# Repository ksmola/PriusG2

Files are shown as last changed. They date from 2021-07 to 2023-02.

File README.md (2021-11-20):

# Prius G2 Inverter controller

## About 

Inverter control board for Toyota Prius Gen 2 (XW20) inverter. 
Some of the schematics are based on Johannes Huebner's work found [here](https://github.com/jsphuebner/inverter-hardware).
Running [openinverter](http://www.openinverter.org) firmware.

    - ESP32 on board
    - AMPSEAL connectors
    - 3D printed enclosure

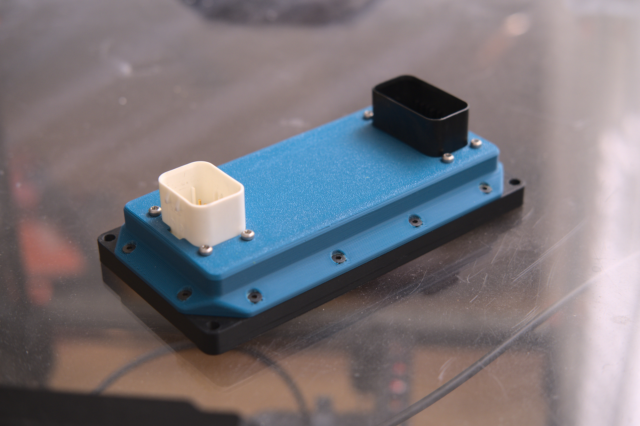
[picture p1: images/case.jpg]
case
 
## Prerequisites 

ESP32 needs [ported webinterface](https://github.com/Bedz01/esp32-web-interface-port)
Get latest openinverter firmware [here](https://github.com/jsphuebner/stm32-sine/releases)

## Pinout 

Pinout is documented on the bottom silk of the PCB

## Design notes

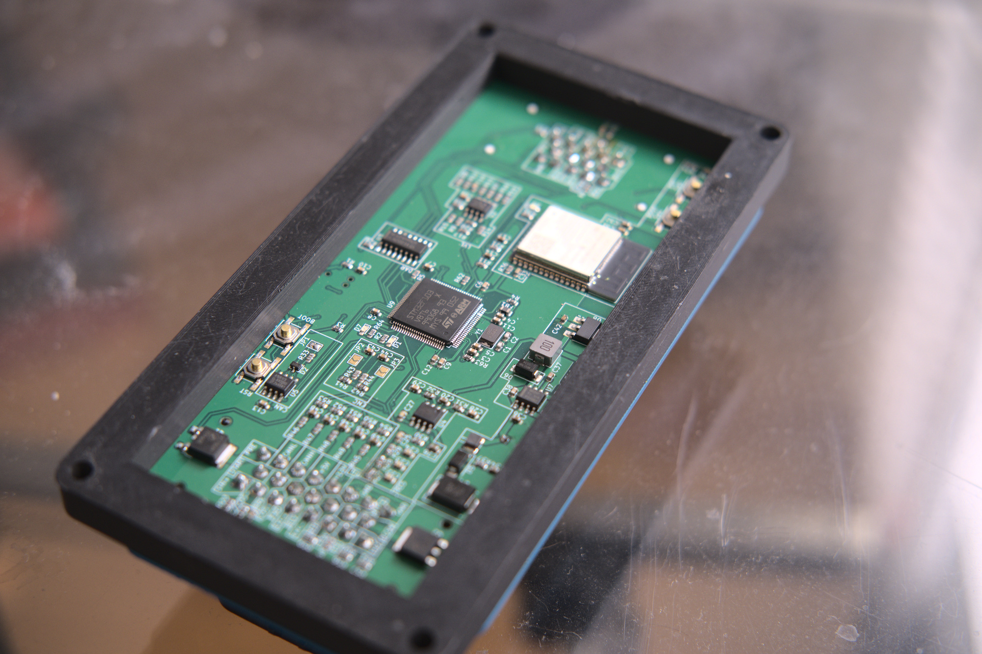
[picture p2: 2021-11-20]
images/board.jpg

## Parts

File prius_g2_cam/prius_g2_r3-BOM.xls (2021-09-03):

Comment | Designator | Package | LCSC Part
0603WAF1201T5E | R54,R53,R52,R51,R50 | R_0603_1608Metric | C22765
SMCJ36CA | D4 | D_SMC | C152081
CL10B102KB8NNNC | C44,C43,C16,C15,C19 | C_0603_1608Metric | C1588
0603WAF2200T5E | R23 | R_0603_1608Metric | C22962
AMS1117-3.3 | U8 | SOT-223-3_TabPin2 | C426566
0603WAF1003T5E | R17,R16,R10,R9,R8,R7 | R_0603_1608Metric | C25803
0603WAF5100T5E | R58,R55,R42,R41,R22 | R_0603_1608Metric | C23193
0603WAF1202T5E | R39 | R_0603_1608Metric | C22790
CL10A475KO8NNNC | C42,C34,C12 | C_0603_1608Metric | C19666
X50328MSB2GI | Y1 | Crystal_SMD_5032-2Pin_5.0x3.2mm | C115962
0603B104K250CT | C13,C11,C10,C9,C8,C7,C6,C5,C4,C3,C38,C29,C28 | C_0603_1608Metric | C83054
0603B104K250CT | C13,C11,C10,C9,C8,C7,C6,C5,C4,C3,C38,C29,C28 | C_0603_1608Metric | C83054
0603B103K500NT | C37 | C_0603_1608Metric | C57112
0603WAF1200T5E | R33 | R_0603_1608Metric | C22787
MWSA0503S-100MT | L2 | MWSA0503 | C408412
PESD1CAN-UX | D2 | SOT-323_SC-70 | C152727
LQH32PN2R2NN0L | L1 | L_1210_3225Metric | C86074
CL10A106KP8NNNC | C41,C40,C18,C32,C26 | C_0603_1608Metric | C19702
MHT192UBCT | D3,D1 | LED_0603_1608Metric_Castellated | C389520
E6Q0603URAC1UDA | D7 | LED_0603_1608Metric_Castellated | C375573
STM32F103VBT6 | U9 | LQFP-100_14x14mm_P0.5mm | C8314
RMC06031K1%N | R35,R2,R64 | R_0603_1608Metric | C269704
0603WAF3302T5E | R14,R12 | R_0603_1608Metric | C4216
LMR14020SDDAR | U7 | SOIC-8-1EP_3.9x4.9mm_P1.27mm_EP2.29x3mm | C187824
ESP32-WROOM-32D | U6 | ESP32-WROOM-32 | C473012
0603WAF3301T5E | R49,R48,R47,R46 | R_0603_1608Metric | C22978
TS-1187A-C-E-B | SW3,SW2,SW1,SW4 | SW_SPST_EVQQ2 | C318887
MCP6022T-I/SN | U2 | SOIC-8-1EP_3.9x4.9mm_P1.27mm_EP2.29x3mm | C57639
ULN2003ADR | U3 | SOIC-16_4.55x10.3mm_P1.27mm | C7512
0603WAF1502T5E | R15,R13 | R_0603_1608Metric | C22809
CL10B104KC8NNNC | C33,C31,C30 | C_0603_1608Metric | C15725
CL10A105KB8NNNC | C36,C20,C52,C51,C50,C49,C48,C47,C46,C45,C17,C14 | C_0603_1608Metric | C15849
CL10B223KB8NNNC | C27,C25,C24,C23,C22 | C_0603_1608Metric | C21122
0603WAF100KT5E | R37 | R_0603_1608Metric | C22936
TDA2822G-S08-R | U4 | SOIC-8-1EP_3.9x4.9mm_P1.27mm_EP2.29x3mm | C73296
CL10C331JB8NNNC | C39 | C_0603_1608Metric | C1664
0603WAF6802T5E | R40 | R_0603_1608Metric | C23231
SS34 | D6,D5 | D_SMA | C8678
AP9T18GH-HF | Q2,Q1 | TO-252-2 | C124546
TJA1051T/3/1J | U5 | SOIC-8_3.9x4.9mm_P1.27mm | C38695
0603WAF1002T5E | R26,R24,R21,R20,R19,R18,R11,R6,R5,R4,R63,R62,R61,R60,R57,R56,R44,R43,R38,R36,R34,R29,R30,R3,R1,R59 | R_0603_1608Metric | C25804
0603WAF4701T5E | R45,R32,R31,R25 | R_0603_1608Metric | C23162
CC0603JRNPO9BN200 | C2,C1 | C_0603_1608Metric | C105621
GZ2012D101TF | FB1 | C_0805_2012Metric | C1015
0603WAF3300T5E | R27 | R_0603_1608Metric | C23138
0603WAF6801T5E | R28 | R_0603_1608Metric | C23212

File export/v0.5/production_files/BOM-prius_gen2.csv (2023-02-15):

Comment | Designator | Footprint | LCSC
Ferrite_Bead | FB1 | C_0805_2012Metric | C1015
20pF | C1,C2 | C_0603_1608Metric | C105621
1uF 12mR | C23,C24 | C_0603_1608Metric | C106858
8MHz | Y1,Y2 | Crystal_SMD_5032-2Pin_5.0x3.2mm | C115962
100n | C16 | C_0603_1608Metric | C14663
SM15T33CA | D4 | D_SMC | C151281
.1uF | C20 | C_0603_1608Metric | C15725
1u | C15,C31,C38,C41 | C_0603_1608Metric | C15849
1n | C13,C14,C17,C39,C40 | C_0603_1608Metric | C1588
100nF | C10,C11,C12,C28,C3,C33,C4,C5,C7,C8,C9 | C_0603_1608Metric | C1590
120pF | C21,C22 | C_0603_1608Metric | C1643
330pF | C34 | C_0603_1608Metric | C1664
4.7uF | C29,C37,C6 | C_0603_1608Metric | C19666
1k | R5,R6 | R_0603_1608Metric | C21190
Q_NPN_BEC | Q1,Q3 | TSOT-23 | C2144
4r7 | R52,R53,R58,R59 | R_0603_1608Metric | C23164
510 | R11,R12,R7,R8 | R_0603_1608Metric | C23193
68k | R19,R20,R29 | R_0603_1608Metric | C23231
2.2uF | C26,C27 | C_0603_1608Metric | C23630
TestPoint | TP1,TP3,TP4,TP5,TP6,TP7,TP8,TP9 | TestPoint_Keystone_5000-5004_Miniature | C238124
1 | R26 | R_0603_1608Metric | C25086
100k | R14 | R_0402_1005Metric | C25741
10k | R1,R10,R13,R16,R18,R2,R22,R23,R27,R3,R30,R35,R42,R45,R46,R9 | R_0603_1608Metric | C25804
17.4k | R24,R51 | R_0603_1608Metric | C269466
10nF | C25,C32 | C_0603_1608Metric | C302008
22pF | C18,C19 | C_0603_1608Metric | C309441
22k | R21 | R_0603_1608Metric | C31850
2k2 | R47,R50,R54,R57 | R_0603_1608Metric | C325643
3r3 | R48,R49,R55,R56 | R_0603_1608Metric | C365471
2.2uH | L1 | L_1210_3225Metric | C36828
LED | D1 | LED_0603_1608Metric_Castellated | C40378
10u | L2 | MWSA0503 | C408412
~ | U9 | SOT-23-6 | C7519
Q_PNP_BEC | Q2,Q4 | TSOT-23 | C8326
D | D10,D7,D8,D9 | D_SOD-123 | C83528
LED | D2 | LED_0603_1608Metric_Castellated | C84264
schottky | D11 | D_SOD-123 | C8598
D_Schottky | D5,D6 | D_SMA | C8678
PESD1CAN-UX | D3 | SOT-323_SC-70 | C907839
AD2S1205YSTZ | U3 | QFP80P1200X1200X160-44N | C91729
10uF | C35,C36 | C_0603_1608Metric | C96446
4K7 | R17 | R_0603_1608Metric | C99782
12k | R28 | R_0603_1608Metric
SW_Push | SW1 | SW_SPST_EVQQ2
TJA1051T-3 | U4 | SOIC-8_3.9x4.9mm_P1.27mm
120 | R25 | R_0603_1608Metric
SW_Push | SW2 | SW_SPST_EVQQ2
SolderJumper_2_Open | JP2 | SolderJumper-2_P1.3mm_Open_TrianglePad1.0x1.5mm
SolderJumper_2_Open | JP3 | SolderJumper-2_P1.3mm_Open_TrianglePad1.0x1.5mm
SolderJumper_2_Open | JP1 | SolderJumper-2_P1.3mm_Open_TrianglePad1.0x1.5mm
AZ1117-3.3 | U6 | SOT-223-3_TabPin2
LMR14020 | U5 | SOIC-8-1EP_3.9x4.9mm_P1.27mm_EP2.29x3mm
MCP602 | U7 | SOIC-8-1EP_3.9x4.9mm_P1.27mm_EP2.29x3mm
100K | R41 | R_0603_1608Metric
10K | R43 | R_0603_1608Metric
100K | R34 | R_0603_1608Metric
33K | R38 | R_0603_1608Metric
33K | R36 | R_0603_1608Metric
15K | R37 | R_0603_1608Metric
100K | R33 | R_0603_1608Metric
100K | R31 | R_0603_1608Metric
100K | R32 | R_0603_1608Metric
15K | R39 | R_0603_1608Metric
100K | R40 | R_0603_1608Metric
10K | R44 | R_0603_1608Metric
ULN2003A | U2 | SOIC-16_4.55x10.3mm_P1.27mm
STM32F407VETx | U1 | LQFP-100_14x14mm_P0.5mm
AD8676xR | U8 | SOIC-8_3.9x4.9mm_P1.27mm
56uF | C30 | CP_Radial_D8.0mm_P3.50mm
Conn_01x23 | J3 | TE_776228-1
Conn_01x06 | J2 | Tag-Connect_TC2030-IDC-NL_2x03_P1.27mm_Vertical
Conn_01x14 | J4 | TE_776262-2
~ | J5 | PinSocket_1x05_P2.54mm_Vertical

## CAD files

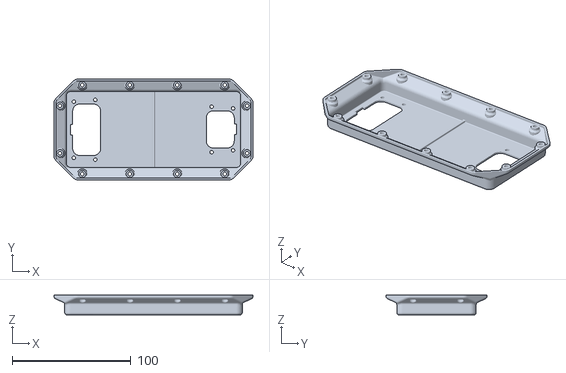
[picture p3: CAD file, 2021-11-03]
case_cad/top_shell.STL
167.8 x 85.0 x 16.7

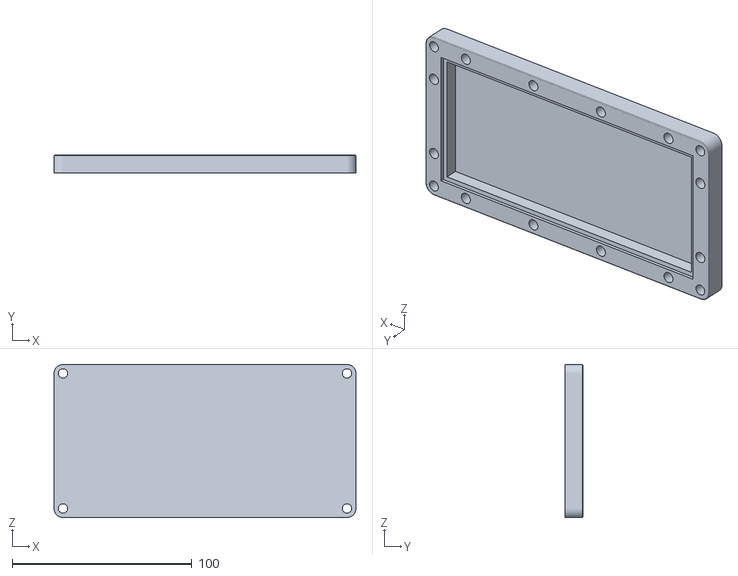
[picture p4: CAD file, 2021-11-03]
case_cad/bottom_frame.STL
167.8 x 10.0 x 85.0

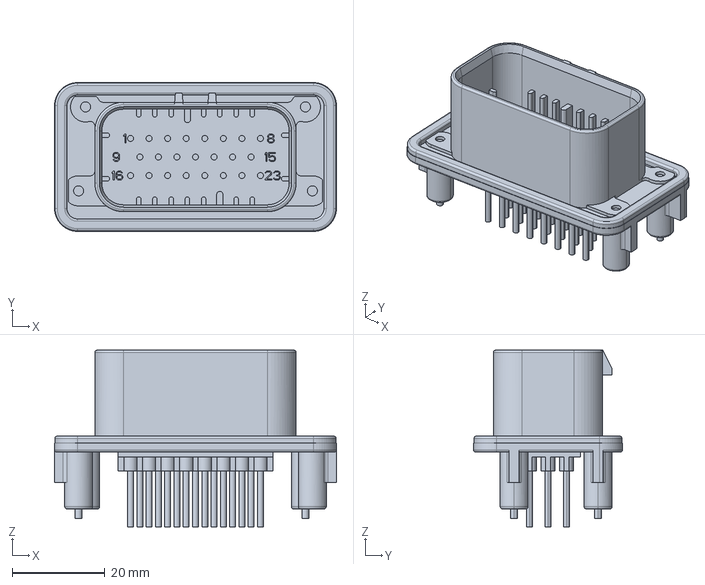
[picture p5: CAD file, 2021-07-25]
case_cad/c-776228-1-e-3d.stp
60.8 x 32.1 x 38.1 mm

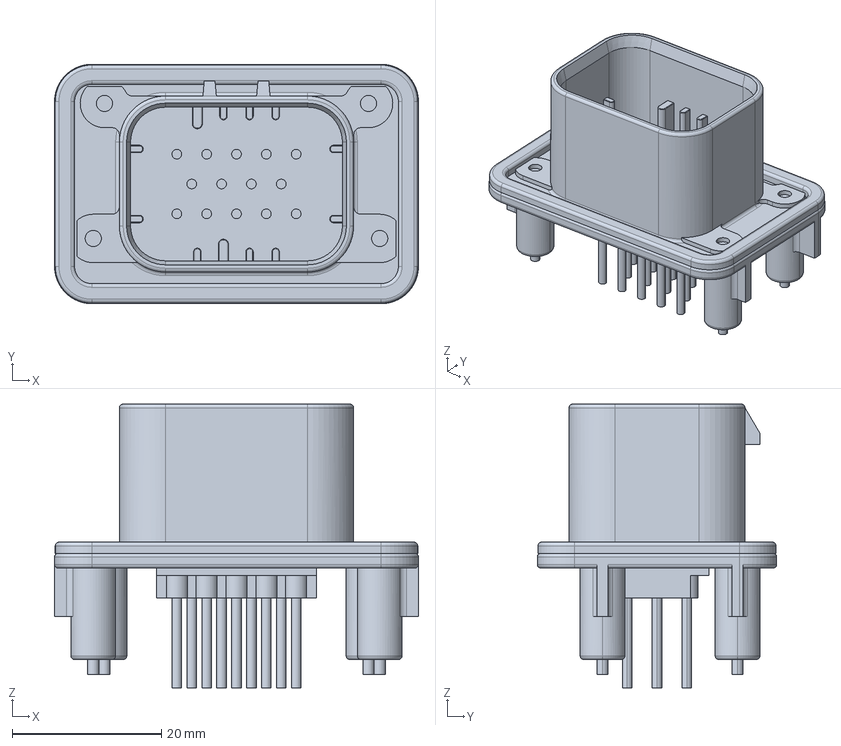
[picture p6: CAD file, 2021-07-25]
case_cad/c-776262-2-c-3d.stp
48.8 x 32.1 x 38.1 mm

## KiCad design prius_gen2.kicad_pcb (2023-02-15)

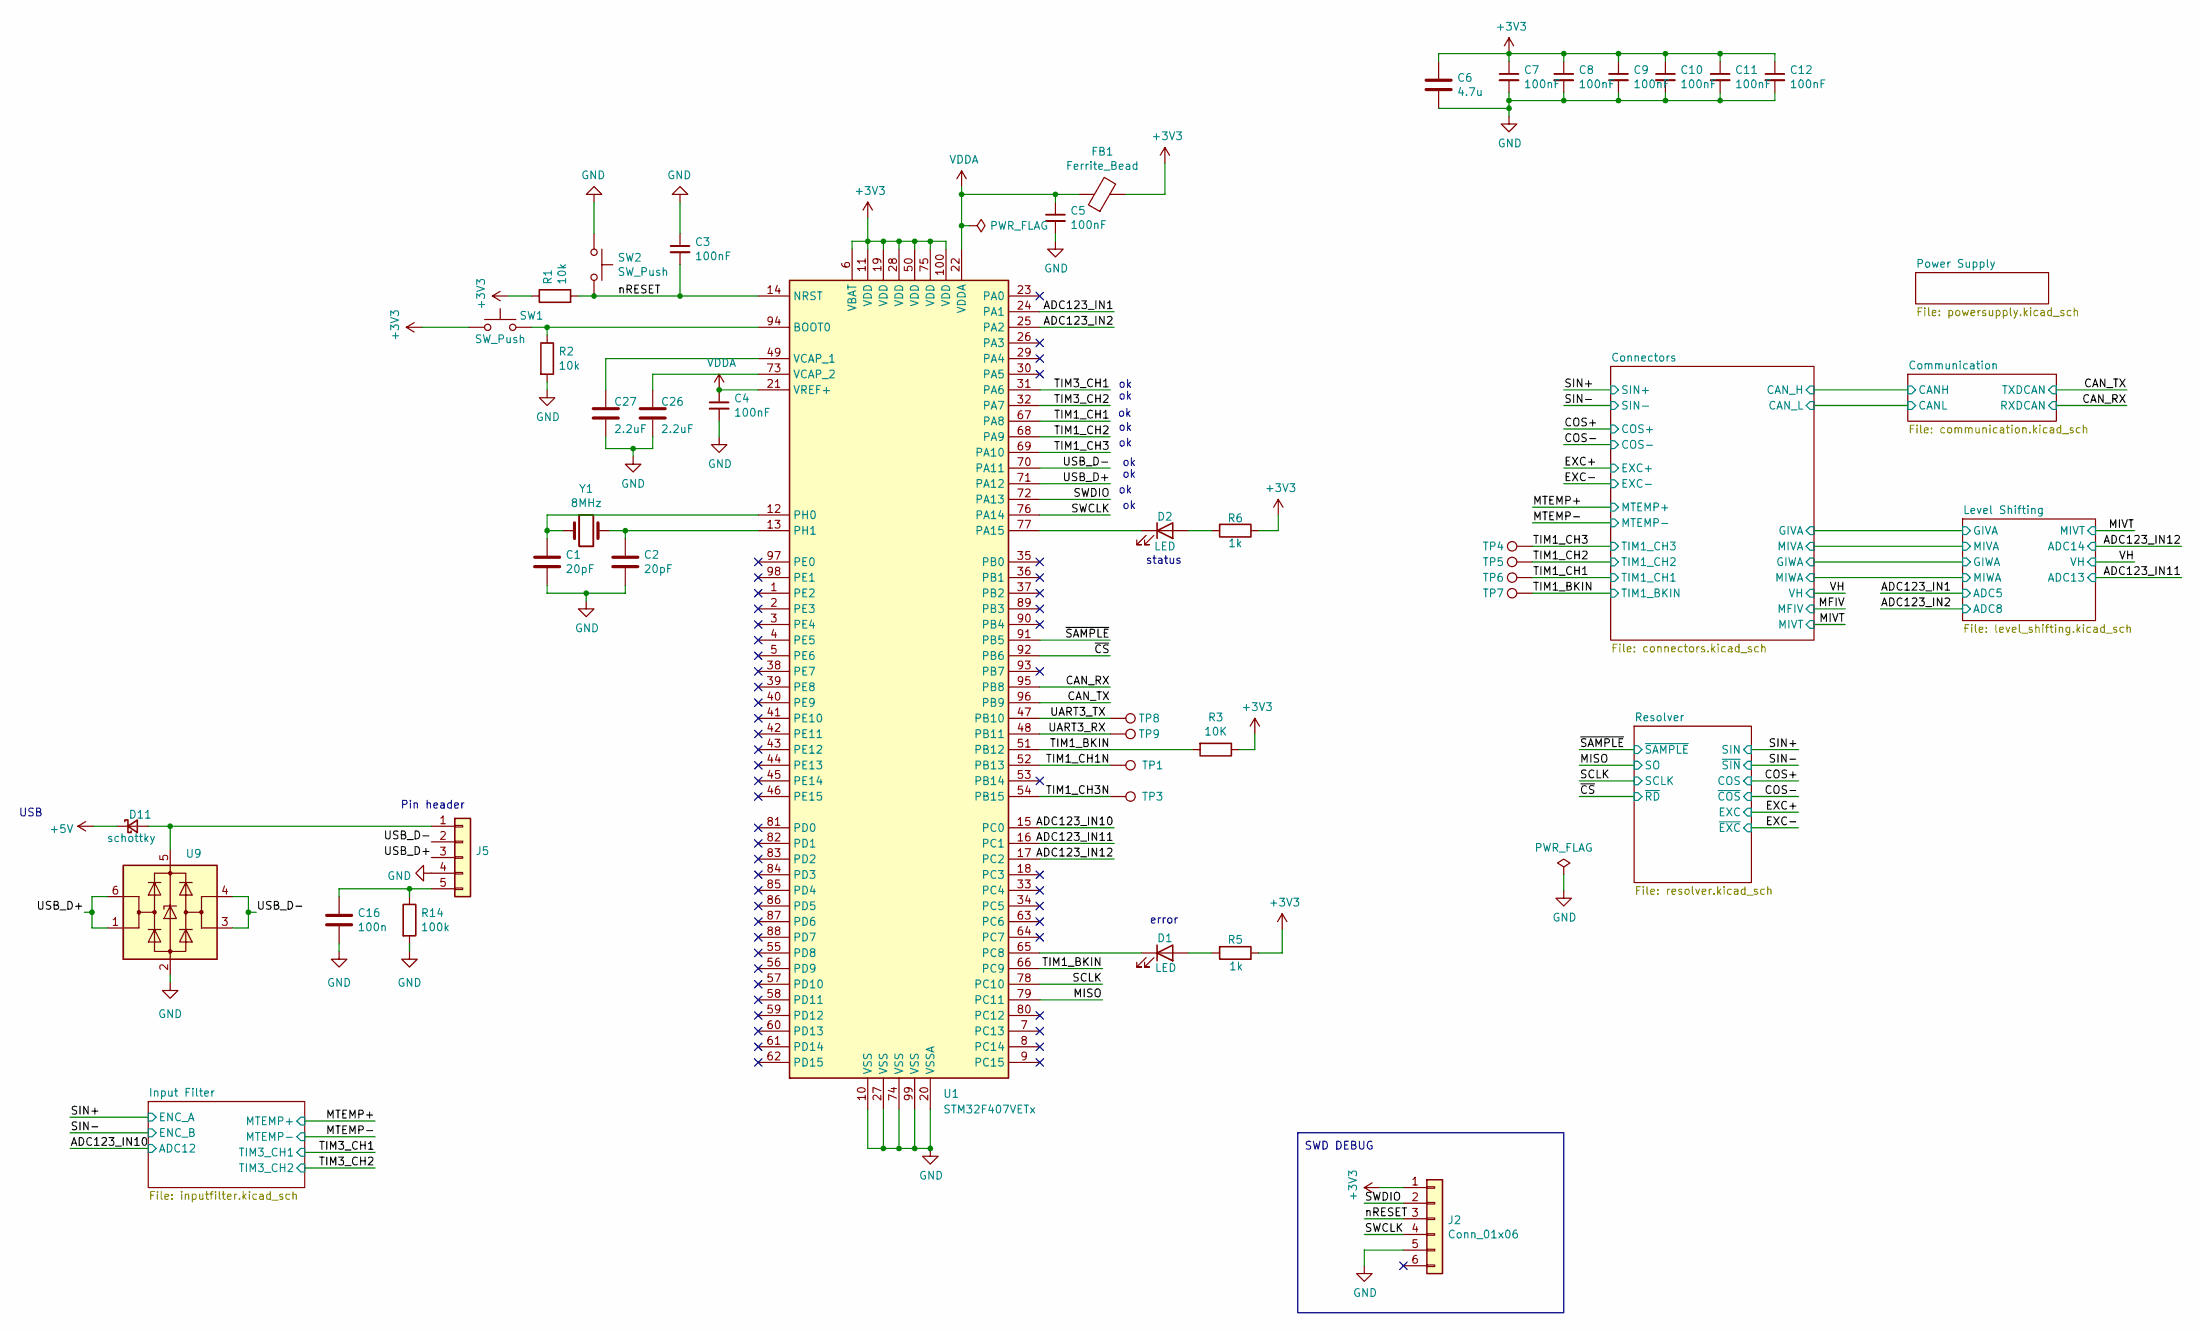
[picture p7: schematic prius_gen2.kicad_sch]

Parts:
C1, C2: 20pF; C_0603_1608Metric; mpn CC0603JRNPO9BN200; LCSC C105621
C3, C4, C5, C7, C8, C9, C10, C11, C12: 100nF; C_0603_1608Metric
C6: 4.7u; C_0603_1608Metric
C16: 100n; C_0603_1608Metric; LCSC C14663
C26, C27: 2.2uF; C_0603_1608Metric; LCSC C23630
D1, D2: LED; LED_0603_1608Metric_Castellated
D11: schottky; D_SOD-123; LCSC C8598
FB1: Ferrite_Bead; C_0805_2012Metric
J2: Conn_01x06; Tag-Connect_TC2030-IDC-NL_2x03_P1.27mm_Vertical
J5: PinSocket_1x05_P2.54mm_Vertical; LCSC N/A
R1, R2: 10k; R_0603_1608Metric; LCSC C25804
R3: 10K; R_0603_1608Metric; LCSC C25804
R5, R6: 1k; R_0603_1608Metric
R14: 100k; R_0402_1005Metric; LCSC C25741
SW1, SW2: SW_Push; SW_SPST_EVQQ2
TP1, TP3, TP4, TP5, TP6, TP7, TP8, TP9: TestPoint; TestPoint_Keystone_5000-5004_Miniature; LCSC C238124
U1: STM32F407VETx; LQFP-100_14x14mm_P0.5mm
U9: SOT-23-6; LCSC C7519
Y1: 8MHz; Crystal_SMD_5032-2Pin_5.0x3.2mm; LCSC C115962

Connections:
+3V3: C6.1, C7.1, C8.1, C9.1, C10.1, C11.1, C12.1, FB1.2, J2.1, R1.1, R3.1, R5.1, R6.1, SW1.1, U1.6 (VBAT), U1.11 (VDD), U1.19 (VDD), U1.28 (VDD), U1.50 (VDD), U1.75 (VDD), U1.100 (VDD); also elsewhere on the board
+5V: D11.1 (K); also elsewhere on the board
/ADC123_IN1: U1.24 (PA1); also elsewhere on the board
/ADC123_IN2: U1.25 (PA2); also elsewhere on the board
/ADC123_IN10: U1.15 (PC0); also elsewhere on the board
/ADC123_IN11: U1.16 (PC1); also elsewhere on the board
/ADC123_IN12: U1.17 (PC2); also elsewhere on the board
/CAN_RX: U1.95 (PB8); also elsewhere on the board
/CAN_TX: U1.96 (PB9); also elsewhere on the board
/MISO: U1.79 (PC11); also elsewhere on the board
/SCLK: U1.78 (PC10); also elsewhere on the board
/SWCLK: J2.4, U1.76 (PA14)
/SWDIO: J2.2, U1.72 (PA13)
/TIM1_BKIN: R3.2, TP7.1, U1.51 (PB12), U1.66 (PC9); also elsewhere on the board
/TIM1_CH1: TP6.1, U1.67 (PA8); also elsewhere on the board
/TIM1_CH1N: TP1.1, U1.52 (PB13)
/TIM1_CH2: TP5.1, U1.68 (PA9); also elsewhere on the board
/TIM1_CH3: TP4.1, U1.69 (PA10); also elsewhere on the board
/TIM1_CH3N: TP3.1, U1.54 (PB15)
/TIM3_CH1: U1.31 (PA6); also elsewhere on the board
/TIM3_CH2: U1.32 (PA7); also elsewhere on the board
/UART3_RX: TP9.1, U1.48 (PB11)
/UART3_TX: TP8.1, U1.47 (PB10)
/USB_D+: J5.3, U1.71 (PA12), U9.1 (I/O1), U9.6 (I/O1)
/USB_D-: J5.2, U1.70 (PA11), U9.3 (I/O2), U9.4 (I/O2)
/nRESET: C3.2, J2.3, R1.2, SW2.2, U1.14 (NRST)
/~CS: U1.92 (PB6); also elsewhere on the board
/~SAMPLE: U1.91 (PB5); also elsewhere on the board
GND: C1.1, C2.1, C3.1, C4.2, C5.2, C6.2, C7.2, C8.2, C9.2, C10.2, C11.2, C12.2, C16.2, C26.2, C27.2, J2.5, J5.4, R2.2, R14.2, SW2.1, U1.10 (VSS), U1.20 (VSSA), U1.27 (VSS), U1.74 (VSS), U1.99 (VSS), U9.2 (GND); also elsewhere on the board
unnamed: D1.2 (A), R5.2
unnamed: D1.1 (K), U1.65 (PC8)
unnamed: D2.2 (A), R6.2
unnamed: D2.1 (K), U1.77 (PA15)
unnamed: D11.2 (A), J5.1, U9.5 (VBUS)
unnamed: C16.1, J5.5, R14.1
unnamed: R2.1, SW1.2, U1.94 (BOOT0)
unnamed: C1.2, U1.12 (PH0), Y1.1
unnamed: C2.2, U1.13 (PH1), Y1.2
unnamed: C27.1, U1.49 (VCAP_1)
unnamed: C26.1, U1.73 (VCAP_2)
VDDA: C4.1, C5.1, FB1.1, U1.21 (VREF+), U1.22 (VDDA)

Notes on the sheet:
USB
status
SWD DEBUG
Pin header
error

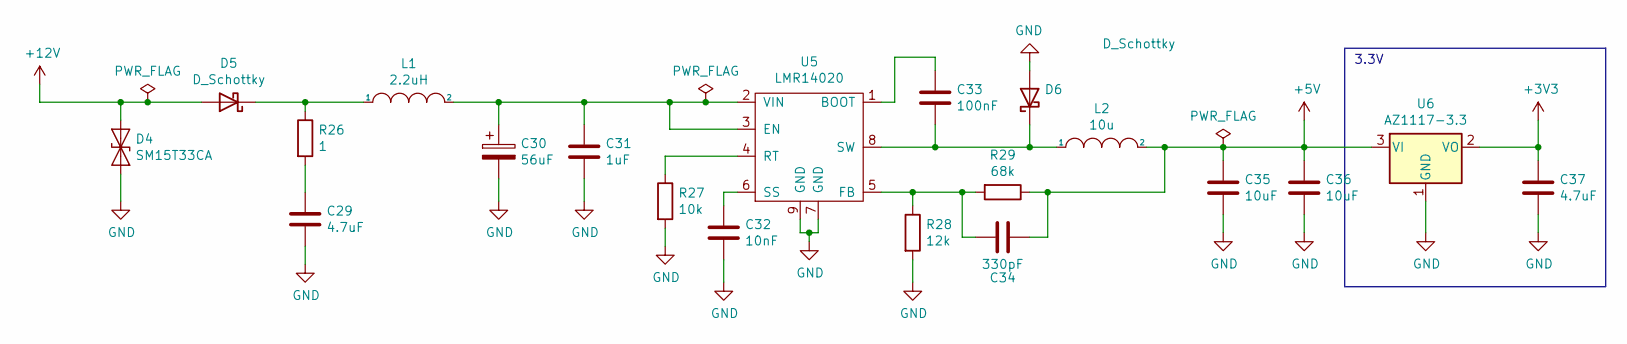
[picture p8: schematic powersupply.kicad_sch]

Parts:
C29, C37: 4.7uF; C_0603_1608Metric
C30: 56uF; CP_Radial_D8.0mm_P3.50mm
C31: 1uF; C_0603_1608Metric
C32: 10nF; C_0603_1608Metric; LCSC C302008
C33: 100nF; C_0603_1608Metric
C34: 330pF; C_0603_1608Metric
C35, C36: 10uF; C_0603_1608Metric
D4: SM15T33CA; D_SMC
D5, D6: D_Schottky; D_SMA
L1: 2.2uH; L_1210_3225Metric
L2: 10u; MWSA0503
R26: 1; R_0603_1608Metric
R27: 10k; R_0603_1608Metric; LCSC C25804
R28: 12k; R_0603_1608Metric
R29: 68k; R_0603_1608Metric; LCSC C23231
U5: LMR14020; SOIC-8-1EP_3.9x4.9mm_P1.27mm_EP2.29x3mm
U6: AZ1117-3.3; SOT-223-3_TabPin2

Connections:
+3V3: C37.1, U6.2 (VO); also elsewhere on the board
+5V: C34.2, C35.1, C36.1, L2.2, R29.1, U6.3 (VI); also elsewhere on the board
+12V: D4.1 (A1), D5.2 (A); also elsewhere on the board
GND: C29.2, C30.2, C31.2, C32.2, C35.2, C36.2, C37.2, D4.2 (A2), D6.2 (A), R27.2, R28.2, U5.7 (GND), U5.9 (GND), U6.1 (GND); also elsewhere on the board
unnamed: C29.1, R26.2
unnamed: D5.1 (K), L1.1, R26.1
unnamed: C33.2, D6.1 (K), L2.1, U5.8 (SW)
unnamed: C33.1, U5.1 (BOOT)
unnamed: C30.1, C31.1, L1.2, U5.2 (VIN), U5.3 (EN)
unnamed: C34.1, R28.1, R29.2, U5.5 (FB)
unnamed: R27.1, U5.4 (RT)
unnamed: C32.1, U5.6 (SS)

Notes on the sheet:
3.3V

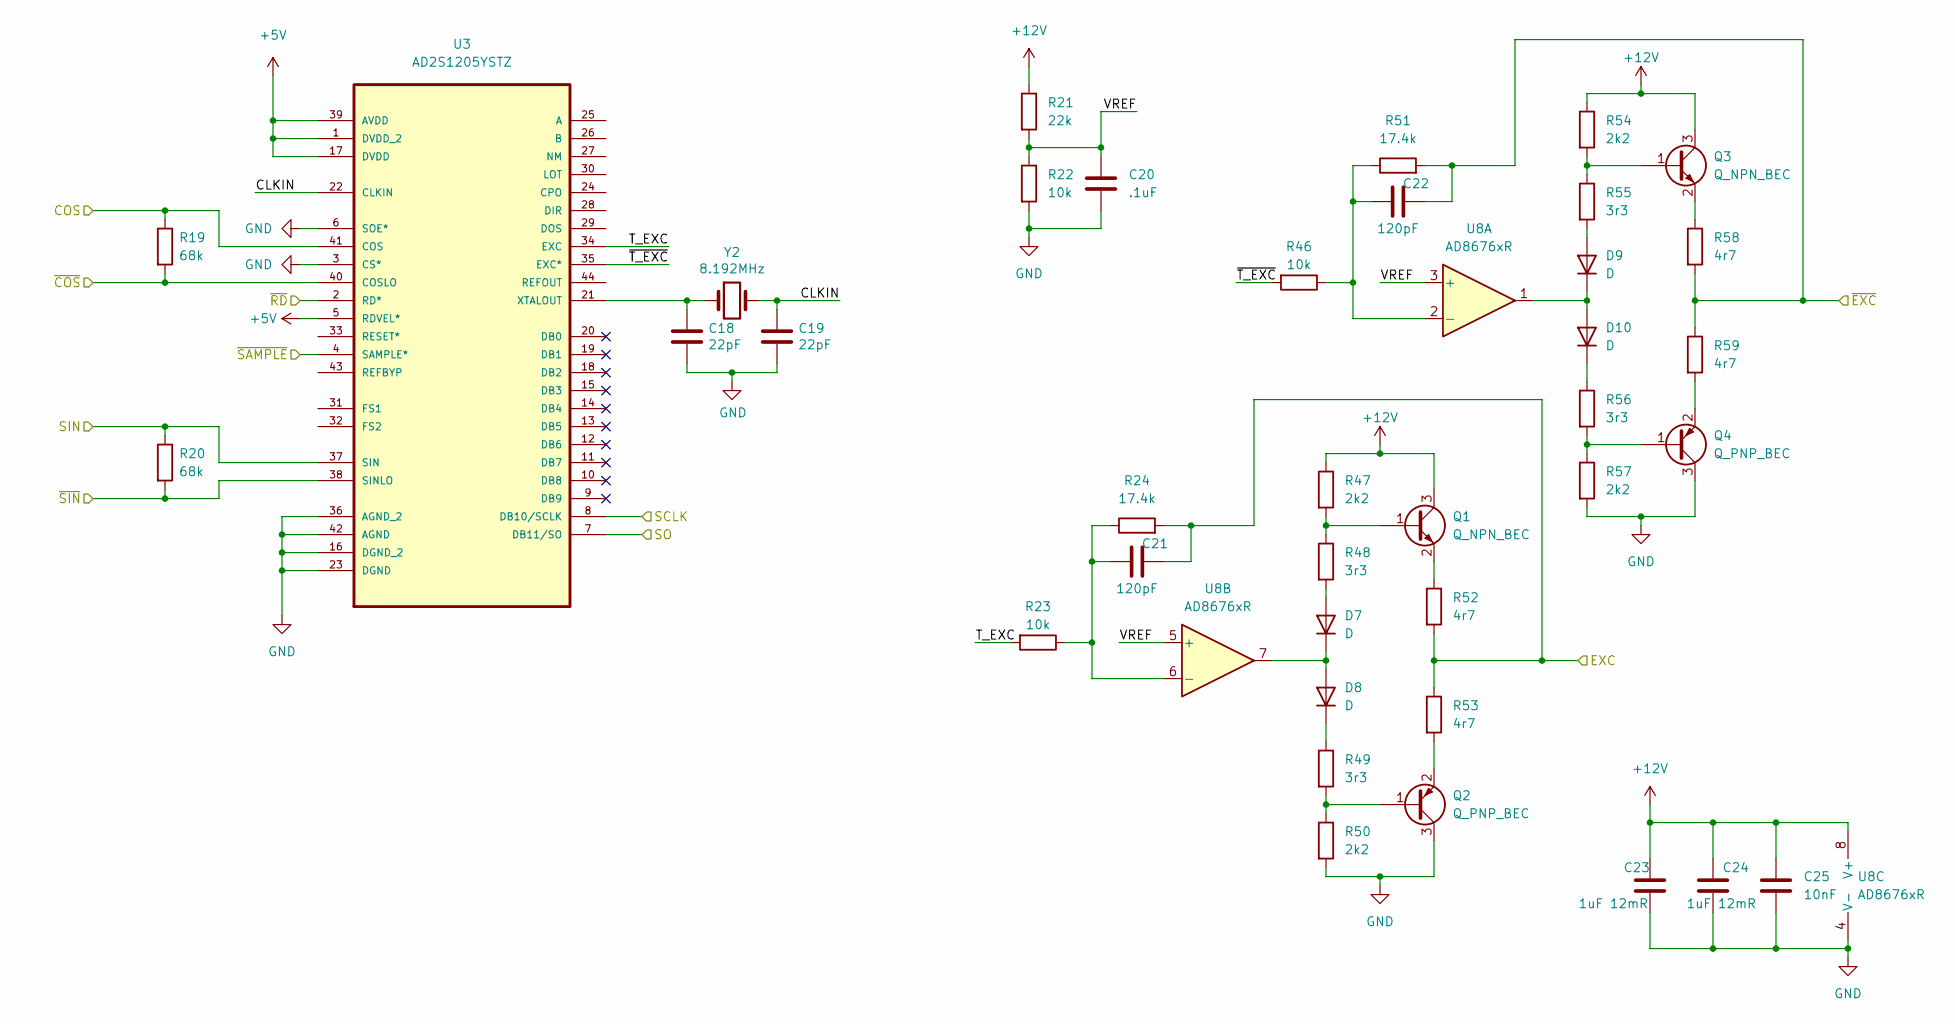
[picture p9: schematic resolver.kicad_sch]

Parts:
C18, C19: 22pF; C_0603_1608Metric; mpn CC0603JRNPO9BN200; LCSC C309441
C20: .1uF; C_0603_1608Metric; LCSC C15725
C21, C22: 120pF; C_0603_1608Metric; LCSC C1643
C23, C24: 1uF 12mR; C_0603_1608Metric; LCSC C106858
C25: 10nF; C_0603_1608Metric; LCSC C302008
D7, D8, D9, D10: D; D_SOD-123; LCSC C83528
Q1, Q3: Q_NPN_BEC; TSOT-23; LCSC C2144
Q2, Q4: Q_PNP_BEC; TSOT-23; LCSC C8326
R19, R20: 68k; R_0603_1608Metric; LCSC C23231
R21: 22k; R_0603_1608Metric
R22, R23, R46: 10k; R_0603_1608Metric; LCSC C25804
R24, R51: 17.4k; R_0603_1608Metric; LCSC C269466
R47, R50, R54, R57: 2k2; R_0603_1608Metric; LCSC C325643
R48, R49, R55, R56: 3r3; R_0603_1608Metric; LCSC C365471
R52, R53, R58, R59: 4r7; R_0603_1608Metric; LCSC C23164
U3: AD2S1205YSTZ; QFP80P1200X1200X160-44N; MPN AD2S1205YSTZ; LCSC C91729
U8: AD8676xR; SOIC-8_3.9x4.9mm_P1.27mm; LCSC C28133
Y2: 8.192MHz; Crystal_SMD_5032-2Pin_5.0x3.2mm; LCSC C115962

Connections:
+5V: U3.1 (DVDD_2), U3.5 (RDVEL*), U3.17 (DVDD), U3.39 (AVDD); also elsewhere on the board
+12V: C23.1, C24.1, C25.1, Q1.3 (C), Q3.3 (C), R21.1, R47.1, R54.1, U8.8 (V+); also elsewhere on the board
/COS+: R19.1, U3.41 (COS); also elsewhere on the board
/COS-: R19.2, U3.40 (COSLO); also elsewhere on the board
/EXC+: C21.2, R24.2, R52.2, R53.1; also elsewhere on the board
/EXC-: C22.2, R51.2, R58.2, R59.1; also elsewhere on the board
/MISO: U3.7 (DB11/SO); also elsewhere on the board
/Resolver/CLKIN: C19.2, U3.22 (CLKIN), Y2.2
/Resolver/T_EXC: R23.2, U3.34 (EXC)
/Resolver/VREF: C20.1, R21.2, R22.1, U8.3 (+), U8.5 (+)
/Resolver/~T_EXC: R46.2, U3.35 (EXC*)
/SCLK: U3.8 (DB10/SCLK); also elsewhere on the board
/SIN+: R20.1, U3.37 (SIN); also elsewhere on the board
/SIN-: R20.2, U3.38 (SINLO); also elsewhere on the board
/~CS: U3.2 (RD*); also elsewhere on the board
/~SAMPLE: U3.4 (SAMPLE*); also elsewhere on the board
GND: C18.1, C19.1, C20.2, C23.2, C24.2, C25.2, Q2.3 (C), Q4.3 (C), R22.2, R50.2, R57.2, U3.3 (CS*), U3.6 (SOE*), U3.16 (DGND_2), U3.23 (DGND), U3.36 (AGND_2), U3.42 (AGND), U8.4 (V-); also elsewhere on the board
unnamed: D7.2 (A), R48.2
unnamed: D7.1 (K), D8.2 (A), U8.7
unnamed: D8.1 (K), R49.1
unnamed: D9.2 (A), R55.2
unnamed: D9.1 (K), D10.2 (A), U8.1
unnamed: D10.1 (K), R56.1
unnamed: Q1.1 (B), R47.2, R48.1
unnamed: Q1.2 (E), R52.1
unnamed: Q2.1 (B), R49.2, R50.1
unnamed: Q2.2 (E), R53.2
unnamed: Q3.1 (B), R54.2, R55.1
unnamed: Q3.2 (E), R58.1
unnamed: Q4.1 (B), R56.2, R57.1
unnamed: Q4.2 (E), R59.2
unnamed: C18.2, U3.21 (XTALOUT), Y2.1
unnamed: C22.1, R46.1, R51.1, U8.2 (-)
unnamed: C21.1, R23.1, R24.1, U8.6 (-)

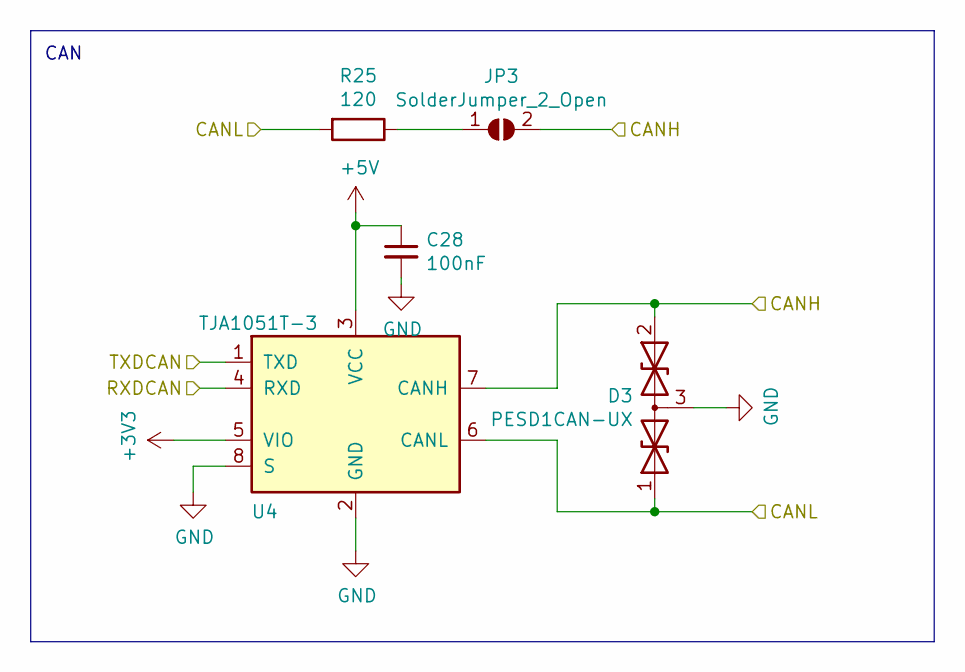
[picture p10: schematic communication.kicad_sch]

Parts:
C28: 100nF; C_0603_1608Metric
D3: PESD1CAN-UX; SOT-323_SC-70
JP3: SolderJumper_2_Open; SolderJumper-2_P1.3mm_Open_TrianglePad1.0x1.5mm
R25: 120; R_0603_1608Metric
U4: TJA1051T-3; SOIC-8_3.9x4.9mm_P1.27mm

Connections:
+3V3: U4.5 (VIO); also elsewhere on the board
+5V: C28.1, U4.3 (VCC); also elsewhere on the board
/CAN_RX: U4.4 (RXD); also elsewhere on the board
/CAN_TX: U4.1 (TXD); also elsewhere on the board
/Communication/CANH: D3.2 (A2), JP3.2 (B), U4.7 (CANH); also elsewhere on the board
/Communication/CANL: D3.1 (A1), R25.2, U4.6 (CANL); also elsewhere on the board
GND: C28.2, D3.3 (common), U4.2 (GND), U4.8 (S); also elsewhere on the board
unnamed: JP3.1 (A), R25.1

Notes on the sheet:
CAN

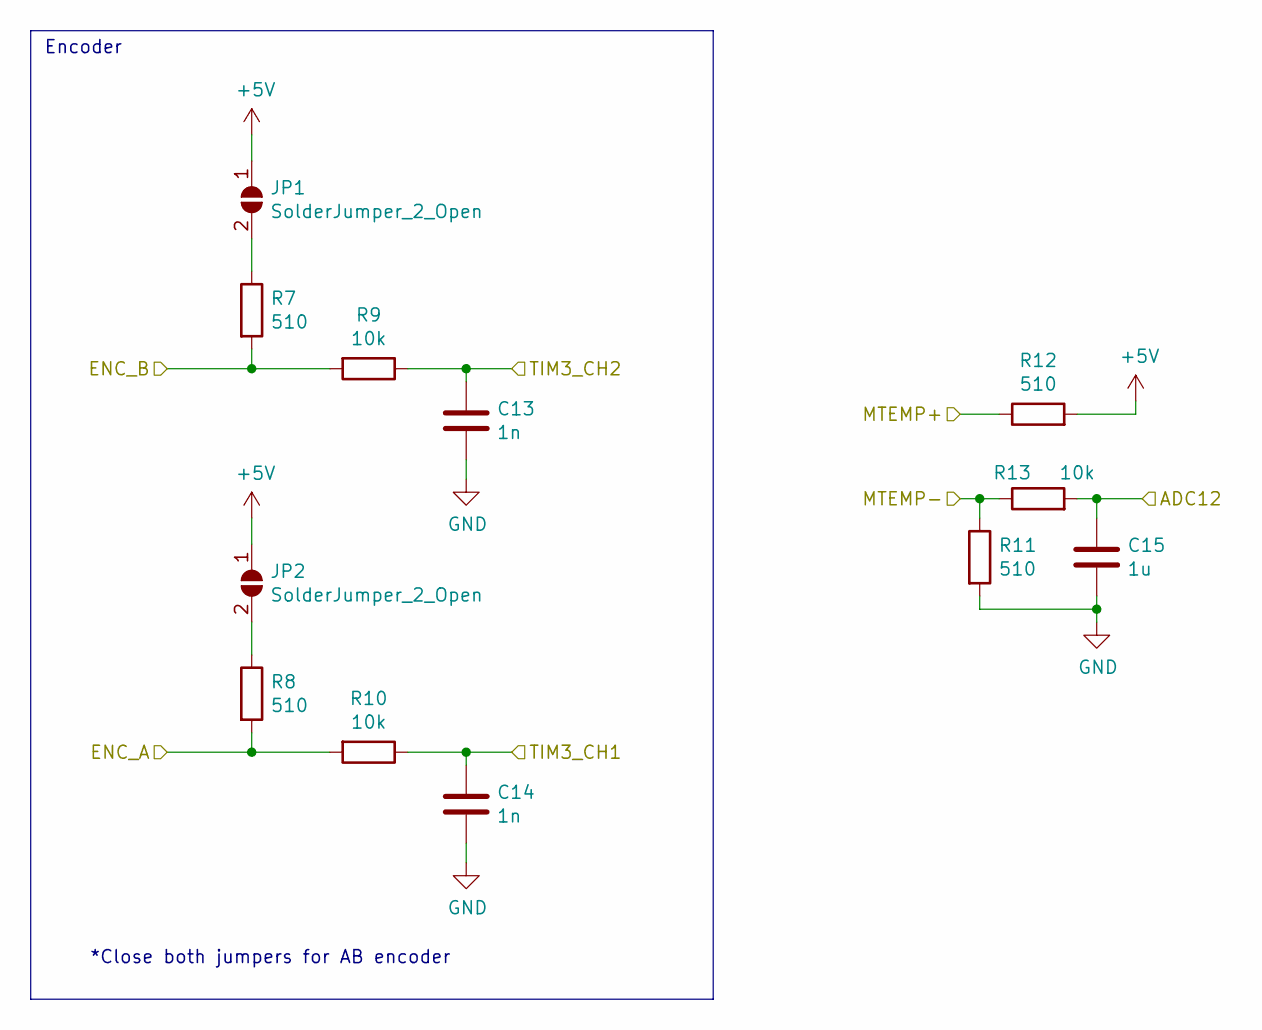
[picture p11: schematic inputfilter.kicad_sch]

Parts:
C13, C14: 1n; C_0603_1608Metric
C15: 1u; C_0603_1608Metric
JP1, JP2: SolderJumper_2_Open; SolderJumper-2_P1.3mm_Open_TrianglePad1.0x1.5mm
R7, R8, R11, R12: 510; R_0603_1608Metric
R9, R10, R13: 10k; R_0603_1608Metric; LCSC C25804

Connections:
+5V: JP1.1 (A), JP2.1 (A), R12.2; also elsewhere on the board
/ADC123_IN10: C15.1, R13.2; also elsewhere on the board
/MTEMP+: R12.1; also elsewhere on the board
/MTEMP-: R11.1, R13.1; also elsewhere on the board
/SIN+: R8.2, R10.2; also elsewhere on the board
/SIN-: R7.2, R9.2; also elsewhere on the board
/TIM3_CH1: C14.1, R10.1; also elsewhere on the board
/TIM3_CH2: C13.1, R9.1; also elsewhere on the board
GND: C13.2, C14.2, C15.2, R11.2; also elsewhere on the board
unnamed: JP1.2 (B), R7.1
unnamed: JP2.2 (B), R8.1

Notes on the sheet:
*Close both jumpers for AB encoder
Encoder

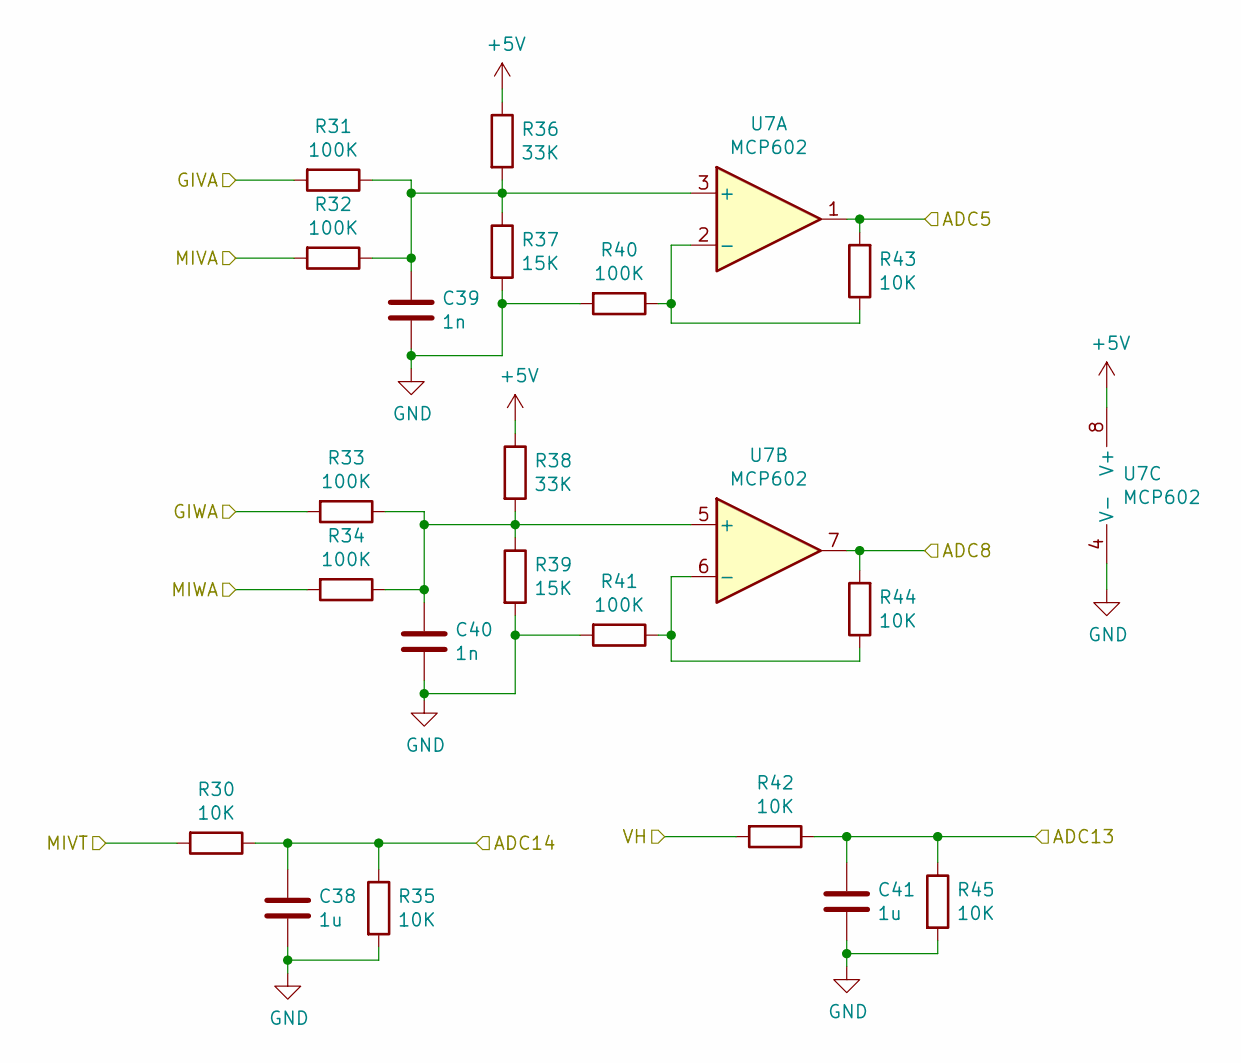
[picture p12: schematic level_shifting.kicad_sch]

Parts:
C38, C41: 1u; C_0603_1608Metric
C39, C40: 1n; C_0603_1608Metric
R30, R35, R42, R45: 10K; R_0603_1608Metric; LCSC C25804
R31, R32, R33, R34, R40, R41: 100K; R_0603_1608Metric
R36, R38: 33K; R_0603_1608Metric
R37, R39: 15K; R_0603_1608Metric
R43, R44: 10K; R_0603_1608Metric
U7: MCP602; SOIC-8-1EP_3.9x4.9mm_P1.27mm_EP2.29x3mm

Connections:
+5V: R36.1, R38.1, U7.8 (V+); also elsewhere on the board
/ADC123_IN1: R43.2, U7.1; also elsewhere on the board
/ADC123_IN2: R44.2, U7.7; also elsewhere on the board
/ADC123_IN11: C41.1, R42.1, R45.1; also elsewhere on the board
/ADC123_IN12: C38.1, R30.1, R35.1; also elsewhere on the board
/Connectors/GIVA: R31.2; also elsewhere on the board
/Connectors/GIWA: R33.2; also elsewhere on the board
/Connectors/MIVA: R32.2; also elsewhere on the board
/Connectors/MIWA: R34.2; also elsewhere on the board
/MIVT: R30.2; also elsewhere on the board
/VH: R42.2; also elsewhere on the board
GND: C38.2, C39.2, C40.2, C41.2, R35.2, R37.2, R39.2, R40.2, R41.2, R45.2, U7.4 (V-); also elsewhere on the board
unnamed: C39.1, R31.1, R32.1, R36.2, R37.1, U7.3 (+)
unnamed: R40.1, R43.1, U7.2 (-)
unnamed: C40.1, R33.1, R34.1, R38.2, R39.1, U7.5 (+)
unnamed: R41.1, R44.1, U7.6 (-)

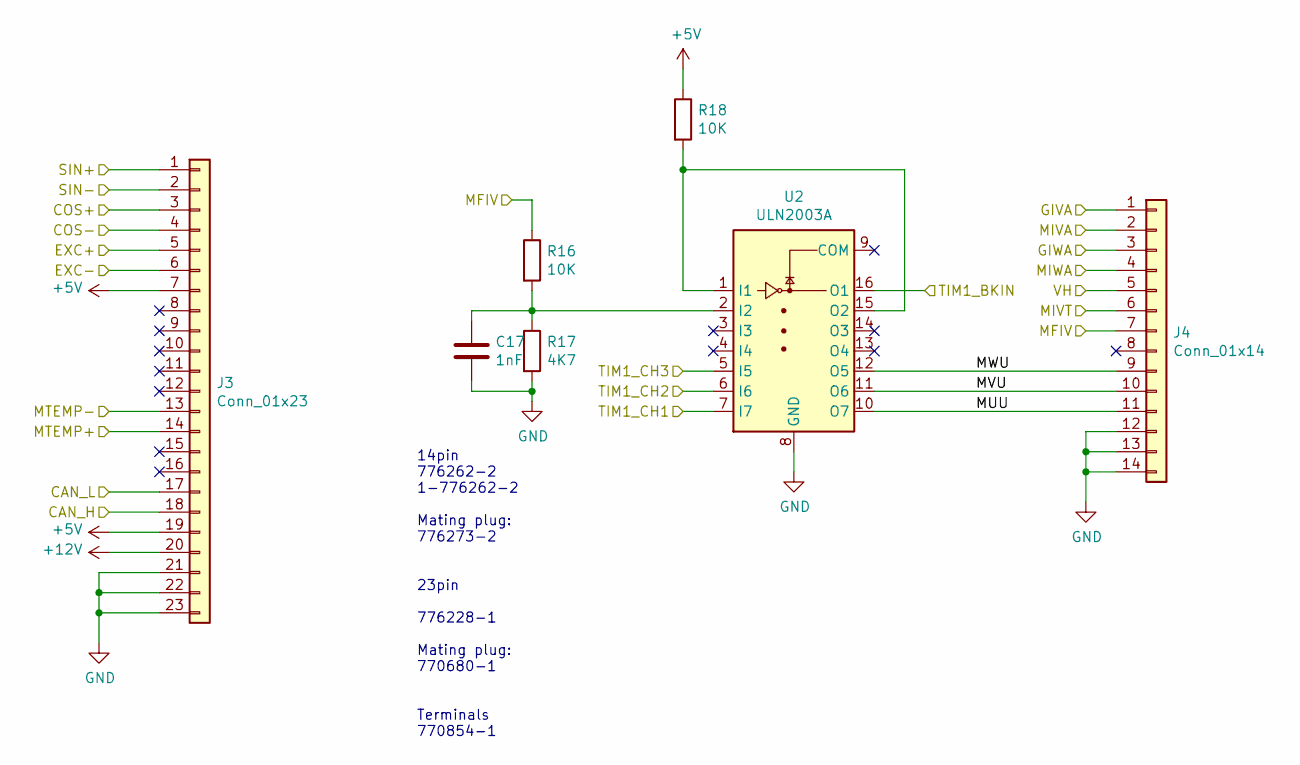
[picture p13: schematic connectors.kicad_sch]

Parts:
C17: 1nF; C_0603_1608Metric
J3: Conn_01x23; TE_776228-1
J4: Conn_01x14; TE_776262-2
R16, R18: 10K; R_0603_1608Metric; LCSC C25804
R17: 4K7; R_0603_1608Metric
U2: ULN2003A; SOIC-16_4.55x10.3mm_P1.27mm

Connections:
+5V: J3.7, J3.19, R18.1; also elsewhere on the board
+12V: J3.20; also elsewhere on the board
/COS+: J3.3; also elsewhere on the board
/COS-: J3.4; also elsewhere on the board
/Communication/CANH: J3.18; also elsewhere on the board
/Communication/CANL: J3.17; also elsewhere on the board
/Connectors/GIVA: J4.1; also elsewhere on the board
/Connectors/GIWA: J4.3; also elsewhere on the board
/Connectors/MIVA: J4.2; also elsewhere on the board
/Connectors/MIWA: J4.4; also elsewhere on the board
/Connectors/MUU: J4.11, U2.10 (O7)
/Connectors/MVU: J4.10, U2.11 (O6)
/Connectors/MWU: J4.9, U2.12 (O5)
/EXC+: J3.5; also elsewhere on the board
/EXC-: J3.6; also elsewhere on the board
/MFIV: J4.7, R16.1
/MIVT: J4.6; also elsewhere on the board
/MTEMP+: J3.14; also elsewhere on the board
/MTEMP-: J3.13; also elsewhere on the board
/SIN+: J3.1; also elsewhere on the board
/SIN-: J3.2; also elsewhere on the board
/TIM1_BKIN: U2.16 (O1); also elsewhere on the board
/TIM1_CH1: U2.7 (I7); also elsewhere on the board
/TIM1_CH2: U2.6 (I6); also elsewhere on the board
/TIM1_CH3: U2.5 (I5); also elsewhere on the board
/VH: J4.5; also elsewhere on the board
GND: C17.2, J3.21, J3.22, J3.23, J4.12, J4.13, J4.14, R17.2, U2.8 (GND); also elsewhere on the board
unnamed: R18.2, U2.1 (I1), U2.15 (O2)
unnamed: C17.1, R16.2, R17.1, U2.2 (I2)

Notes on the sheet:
14pin 776262-2 1-776262-2 Mating plug: 776273-2 23pin 776228-1 Mating plug: 770680-1 Terminals 770854-1

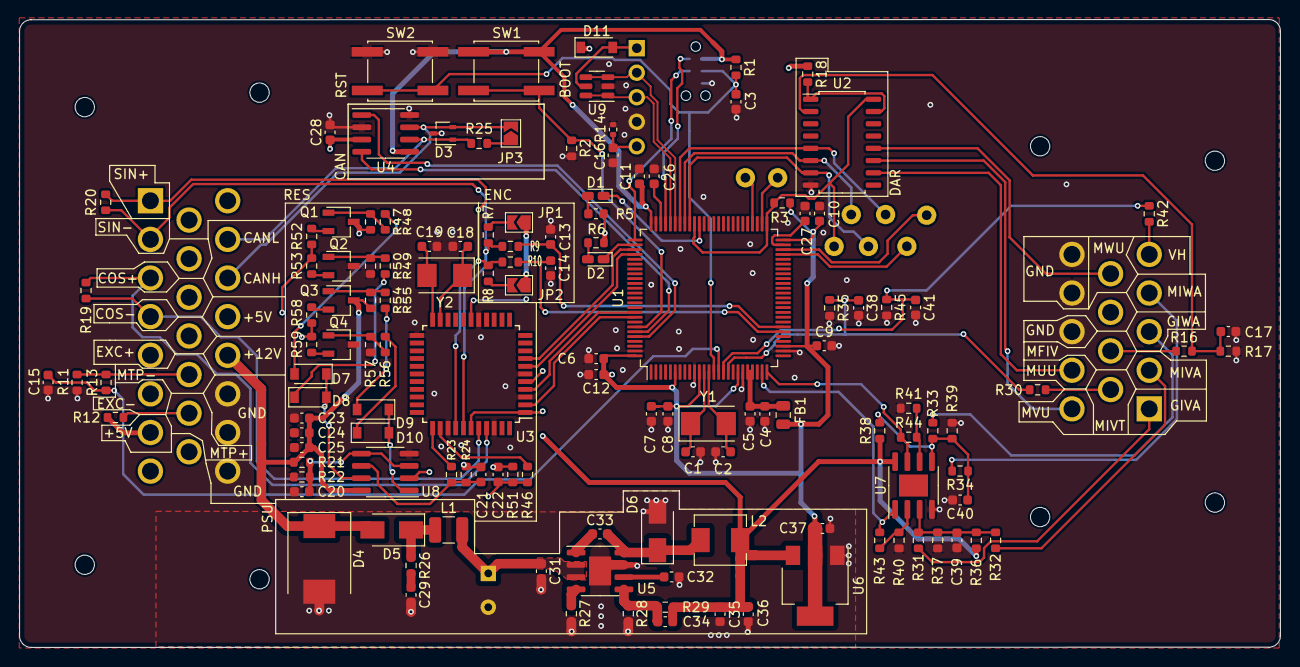
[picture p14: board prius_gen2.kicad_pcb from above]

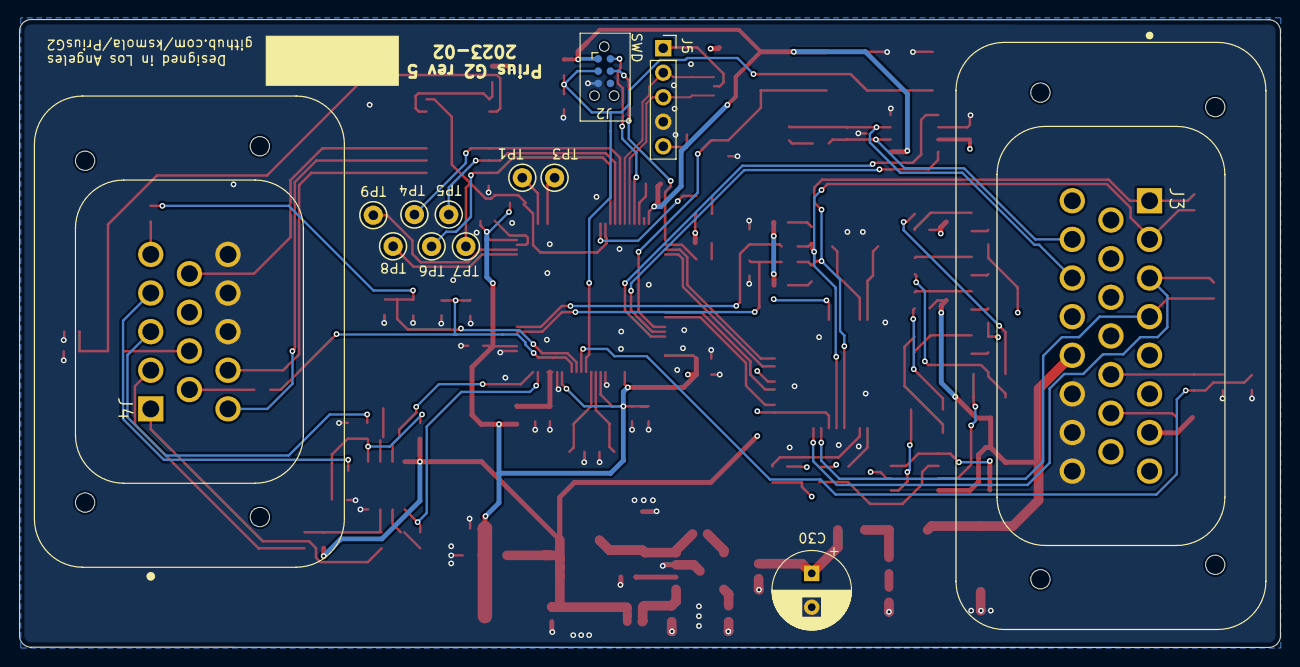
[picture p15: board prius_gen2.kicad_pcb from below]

Board: 4 copper layers, 130.6 x 65.0 mm, 144 parts (13 on the bottom side), 100 nets.

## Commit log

2021-07-25 iniial commit...
    [c-776228-1-e-3d.stp, c-776262-2-c-3d.stp, communication.sch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]
2021-07-26 CAD case
    [c-776228-1-e-3d.stp, c-776262-2-c-3d.stp]
2021-08-04 fixed schematics error
    [communication.sch, connectors.sch, inputfilter.sch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]
2021-08-04 updated routing
    [prius_gen2.kicad_pcb]
2021-08-04 more routing fixes
    [prius_gen2.kicad_pcb]
2021-08-05 updated silk and manuf. files
    [prius_g2_bom.xls, prius_g2_r3-BOM.xls, prius_gen2.kicad_pcb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]
2021-08-05 fixed bom
    [prius_g2_r3-BOM.xls]
2021-08-30 updated vals for 3stage RC filter
    [prius_g2_r3-BOM.xls, resolver.sch]
2021-09-03 more updates to RC filter; fixed pinout silk
    [prius_g2_r3-BOM.xls, prius_gen2.kicad_pcb, resolver.sch]
2021-11-03 updated resolver schematics
    [resolver.sch]
2021-11-03 updates for release
    [prius_gen2.kicad_pcb]
2021-11-03 added case stl
    [bottom_frame.STL, top_shell.STL]
2022-12-24 updates for KiCAD 6
    [communication.kicad_sch, connectors.kicad_sch, inputfilter.kicad_sch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]
2022-12-26 started adding AD2S
    [communication.kicad_sch, connectors.kicad_sch, inputfilter.kicad_sch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]
2022-12-27 routed ad2s
    [connectors.kicad_sch, inputfilter.kicad_sch, level_shifting.kicad_sch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]
2022-12-27 cleaned up board
    [prius_gen2.kicad_pcb, prius_gen2.kicad_sch]
2022-12-29 fixed resolver buffer circuit
    [prius_gen2.kicad_pcb, prius_gen2.kicad_sch, resolver.kicad_sch]
2023-01-01 added USB
    [prius_gen2.kicad_pcb, prius_gen2.kicad_sch, resolver.kicad_sch]
2023-01-01 v0.4 manufactoring files
    [bom.csv, positions.csv, prius_gen2.kicad_pcb]
2023-01-25 fixes for v5
    [communication.kicad_sch, connectors.kicad_sch, inputfilter.kicad_sch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]
2023-01-26 fixed some drc errors
    [prius_gen2.kicad_pcb]
2023-02-13 more updates for v0.5 prod
    [communication.kicad_sch, connectors.kicad_sch, inputfilter.kicad_sch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]
2023-02-14 fixed adcs
    [prius_gen2.kicad_pcb, prius_gen2.kicad_sch]
2023-02-15 v0.5 production files
    [BOM-prius_gen2.csv, powersupply.kicad_sch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]
